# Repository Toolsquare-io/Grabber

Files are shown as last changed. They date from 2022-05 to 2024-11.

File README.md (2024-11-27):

# Tha Grabber
A machine to show what we can do with our [Toolsquare](www.toolsquare.io) units. 

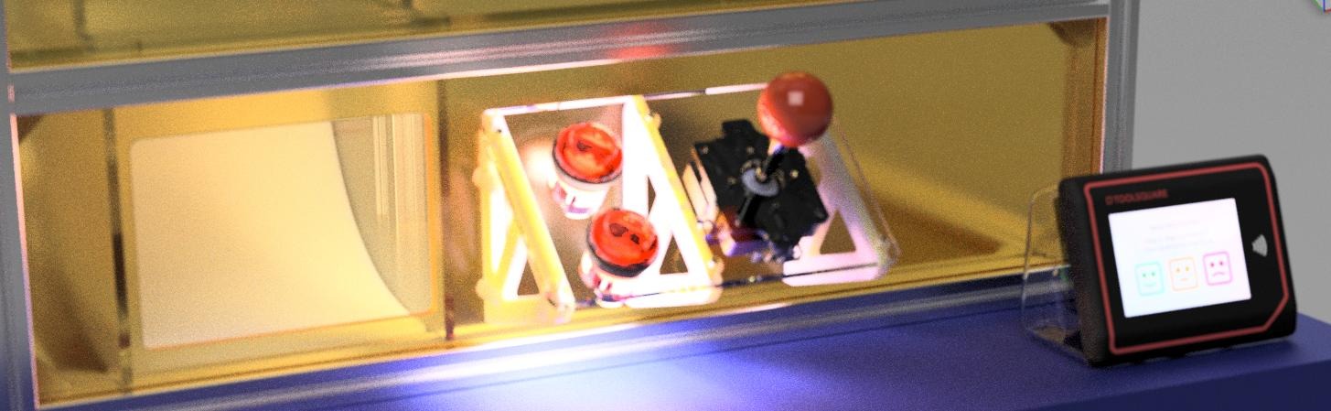
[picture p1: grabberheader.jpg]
Fusion render


## Timeline
### Deadline
* [Laborama](https://expo.laborama.be/nl/) 19 & 20 mei
* [Nerdland](https://www.nerdlandfestival.be/) 3, 4 & 5 juni

### Build timeline
* CAD approval -> 8th of April
---

**Everything below is draft and could change, keep those affected in the loop!**

---

## Requirements
* Dimensions footprint: 60x60cm
* Should reflect a Toolsquare machine: locked, idle, running. 
* Gadget max dimension: 14x12cm, height 7cm
* Should be easy to install by one person
* Should be able to run without supervision (so not too easy to break in) 
* Lights!

## The game
1. Unlock the machine using a Toolsquare unit or something else (a coin, a simple nfc reader,..)
2. Use the joystick to positon X and Y
3. Press a button to auto **lower the grabber, raise and dump the gadget**
5. Once a timout is reached the crane goes back to home and needs to be unlocked again

## BOM
The full [BOM](https://docs.google.com/spreadsheets/d/1Js6a-A9pP3j60k_G_hthX2zwbCBgAsaMytp7D8mz5XA/edit?usp=sharing)
* [Bosch-Rexroth](https://benl.rs-online.com/web/c/engineering-materials-industrial-hardware/structural-systems/) and connections
* [Optional Neopixels](https://www.adafruit.com/product/1138?length=1)
* ESP32
* [Linear Bearings](https://benl.rs-online.com/web/p/products/2346942/)
* [Linear Guide](https://benl.rs-online.com/web/p/products/4485449/) and cariage (https://benl.rs-online.com/web/p/products/3752445/)
* [Motors](https://www.amazon.nl/gp/product/B06Y2BSCL7/ref=ppx_yo_dt_b_asin_title_o00_s00?ie=UTF8&psc=1)

## CAD
[The Fusion model](https://a360.co/3V7IlZC)

## Inspirations
[CoreXY](http://corexy.com/theory.html)

CoreXY Math

## Electronics

Pinouts
CNCShield pinmapping

|  Function | Pin Number |  
|---|---|
|  Stepper X | |  
|  Stepper Y |  |  
|  Stepper Z  |  | 
|  Interlock X |  | 
|  Interlock Y  |  | 
|  Interlock Z  |  | 
|  JoyStick X  |  | 
|  JoyStick Y  |  |  
|  Button 1  |  | 
|  Button 2  |  | 
|  Button 1 LED  |  |
|  Button 2 LED  |  | 
|  NeoPixel  |  | 
|  Running Out  |  | 
|  Machine Lock  |  | 
|  Magnet Relais  |  |

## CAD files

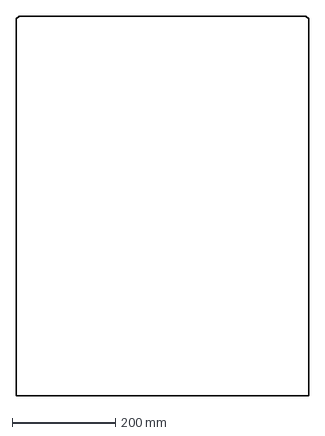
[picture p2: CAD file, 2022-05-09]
cad/production/TopFrontPlate.dxf
567.0 x 737.0 mm

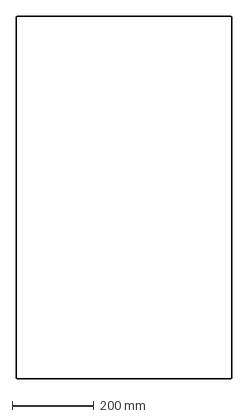
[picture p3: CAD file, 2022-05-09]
cad/production/RightPlate.dxf
527.0 x 887.0 mm

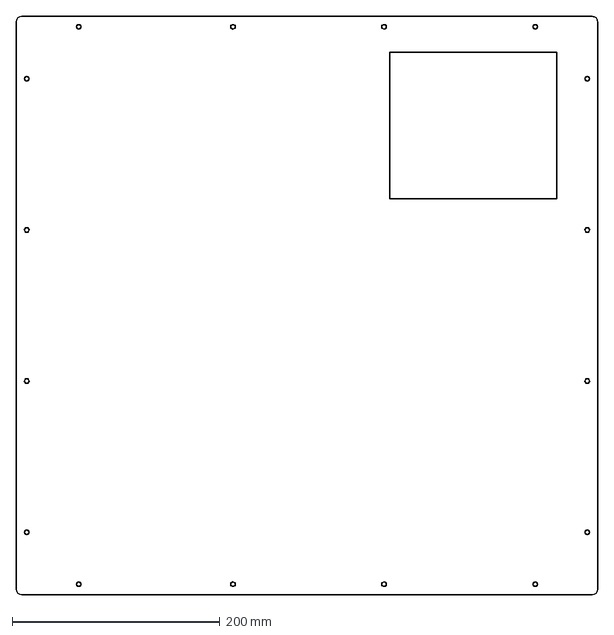
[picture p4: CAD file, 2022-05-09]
cad/production/GadgetFloorPlate.dxf
560.0 x 557.0 mm

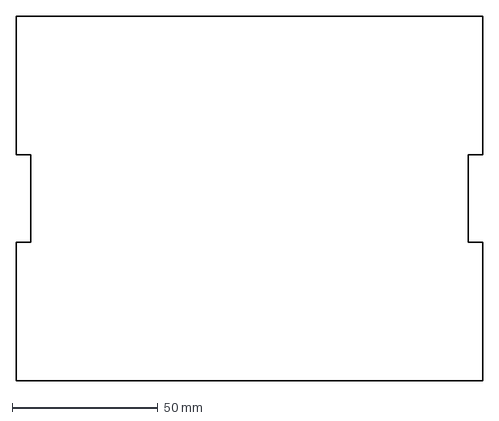
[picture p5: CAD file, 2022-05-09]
cad/production/GadgetTowerFront.dxf
160.0 x 125.0 mm

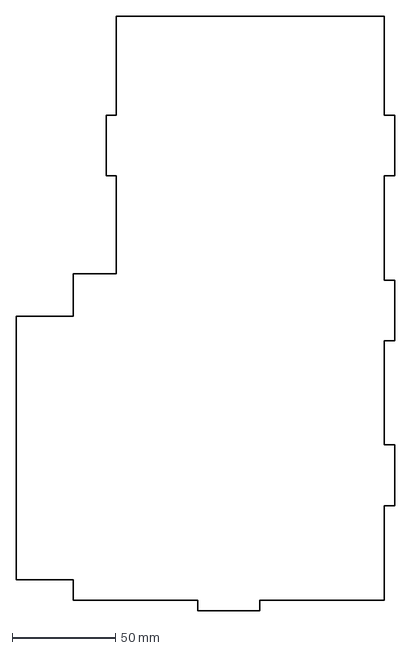
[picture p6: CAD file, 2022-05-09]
cad/production/GadgetTowerRight.dxf
183.5 x 288.5 mm

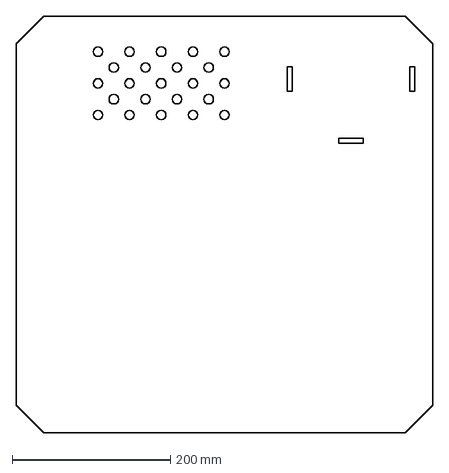
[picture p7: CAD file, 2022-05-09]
cad/production/BottomPlate.dxf
527.0 x 527.0 mm

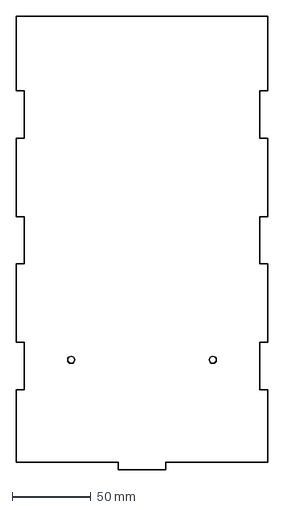
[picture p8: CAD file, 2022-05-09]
cad/production/GadgetTowerBack.dxf
160.0 x 288.5 mm

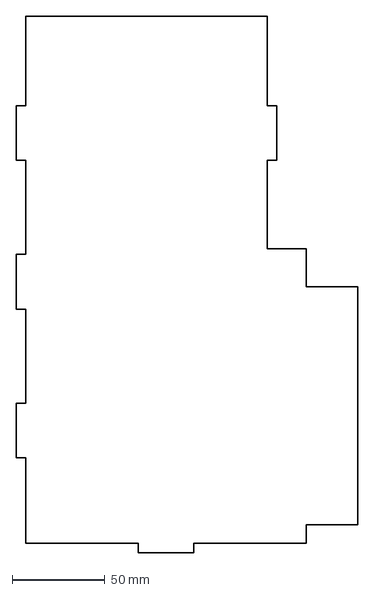
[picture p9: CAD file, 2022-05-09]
cad/production/GadgetTowerLeft.dxf
183.5 x 288.5 mm

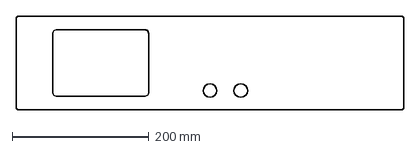
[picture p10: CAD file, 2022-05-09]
cad/production/FixedFrontPlate.dxf
567.0 x 137.0 mm

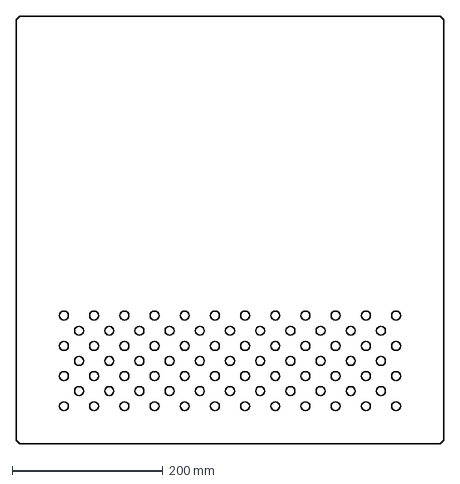
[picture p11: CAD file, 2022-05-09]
cad/production/TopPlate.dxf
567.0 x 567.0 mm

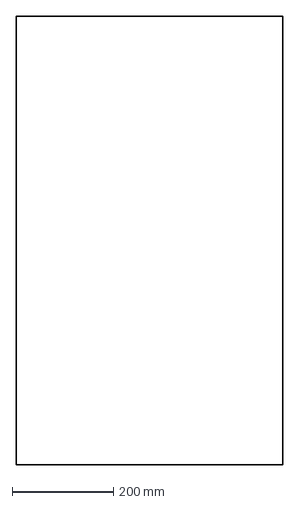
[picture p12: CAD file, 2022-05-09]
cad/production/LeftPlate.dxf
527.0 x 887.0 mm

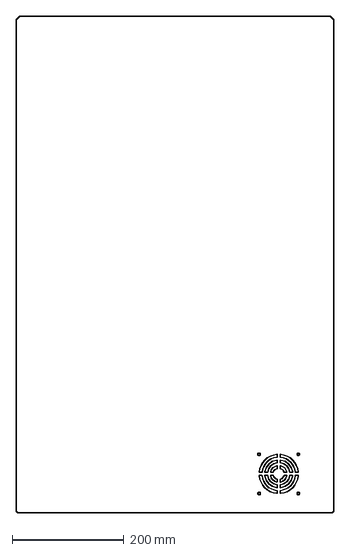
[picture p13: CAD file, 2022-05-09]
cad/production/BackPlate.dxf
568.0 x 888.0 mm

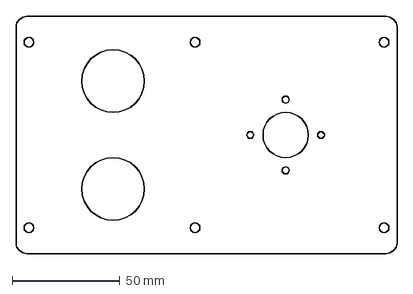
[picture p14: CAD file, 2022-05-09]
cad/production/Controller.dxf
176.6 x 110.0 mm

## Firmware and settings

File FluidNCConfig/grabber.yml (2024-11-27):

board: TMC2209 4X
name: TMC2209 XYZA
stepping:
  engine: I2S_STREAM
  idle_ms: 255
  pulse_us: 2
  dir_delay_us: 1
  disable_delay_us: 0

kinematics:
  corexy:

i2so:
  bck_pin: gpio.22
  data_pin: gpio.21
  ws_pin: gpio.17

axes:
  shared_stepper_disable_pin: NO_PIN
  
  x:
    steps_per_mm: 100
    max_rate_mm_per_min: 5000
    acceleration_mm_per_sec2: 100
    max_travel_mm: 298
    soft_limits: true
    homing:
      cycle: 2
      mpos_mm: 0
      positive_direction: false
      feed_mm_per_min: 400.000
      seek_mm_per_min: 1200.000
      settle_ms: 200
    
    motor0:
      limit_pos_pin: gpio.36:low
      hard_limits: false
      pulloff_mm: 10.000
      tmc_2209:
        uart:
          txd_pin: gpio.16
          rxd_pin: gpio.4
          baud: 115200
          mode: 8N1
        addr: 0
        r_sense_ohms: 0.110
        run_amps: 0.500
        hold_amps: 0.250
        microsteps: 16
        stallguard: 0
        stallguard_debug: true
        toff_disable: 0
        toff_stealthchop: 5
        toff_coolstep: 3
        run_mode: StealthChop
        homing_mode: StealthChop
        use_enable: true
        step_pin: i2so.2
        direction_pin: i2so.1
        disable_pin: i2so.0

    motor1:
      null_motor:

  y:
    steps_per_mm: 100
    max_rate_mm_per_min: 5000
    acceleration_mm_per_sec2: 100
    max_travel_mm: 325
    soft_limits: true

    homing:
      cycle: 3
      mpos_mm: 0
      positive_direction: false
      feed_mm_per_min: 400.000
      seek_mm_per_min: 1200.000
      settle_ms: 200
    
    motor0:
      limit_pos_pin: gpio.39:low
      hard_limits: false
      pulloff_mm: 10.00
      tmc_2209:
        addr: 1
        r_sense_ohms: 0.110
        run_amps: 0.500
        hold_amps: 0.250
        microsteps: 16
        stallguard: 0
        stallguard_debug: false
        toff_disable: 0
        toff_stealthchop: 5
        toff_coolstep: 3
        run_mode: StealthChop
        homing_mode: StealthChop
        use_enable: true
        step_pin: i2so.5
        direction_pin: i2so.4
        disable_pin: i2so.7

    motor1:
      null_motor:

  z:
    steps_per_mm: 100
    max_rate_mm_per_min: 5000
    acceleration_mm_per_sec2: 100
    max_travel_mm: 135
    soft_limits: true

    homing:
      cycle: 1
      mpos_mm: 0
      positive_direction: true
      feed_mm_per_min: 200.000
      seek_mm_per_min: 600.000
      settle_ms: 200

    motor0:
      limit_pos_pin: gpio.34:low
      hard_limits: false
      pulloff_mm: 10.000
      tmc_2209:
        addr: 2
        r_sense_ohms: 0.110
        run_amps: 0.500
        hold_amps: 0.250
        microsteps: 16
        stallguard: 0
        stallguard_debug: false
        toff_disable: 0
        toff_stealthchop: 5
        toff_coolstep: 3
        run_mode: StealthChop
        homing_mode: StealthChop
        use_enable: true
        step_pin: i2so.10
        direction_pin: i2so.9
        disable_pin: i2so.8

    motor1:
      null_motor:

spi:
  miso_pin: gpio.19
  mosi_pin: gpio.23
  sck_pin: gpio.18

sdcard:
  cs_pin: gpio.5
  card_detect_pin: NO_PIN

start:
  must_home: true

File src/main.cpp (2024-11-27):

#include <Arduino.h>
#include "logging.h"
#include "machineinputs.h"
#include "pinmapping.h"
#include "ledmadness.h"
#include "inputstates.h"

// creating the objects
uLog theLog;
machineInputs theInput;
pinmapping thePins;
ledmadness theLeds;

// forward declarations
// void echoSerial();
bool outputToSerial(const char* contents);
bool loggingTime(char* contents, uint32_t length);
void printHeartBeat();

void setup() {
    // configure output
    theLog.setColoredOutput(0U, true);        // enable colored output - remember to set 'monitor_flags = --raw' in platformio.ini    theLog.output(subSystem::general, loggingLevel::Error, "This is an error");           //
    Serial.begin(112500);
    Serial1.begin(115200);
    Serial1.setTimeout(50);
    theLog.setOutput(0U, outputToSerial);
    theLog.outputIsActive(true);

    // setting logginlevels
    theLog.setLoggingLevel(0U, loggingLevel::Debug);

    // setup start
    theLog.output(subSystem::general, loggingLevel::Info, "starting");        //

    theInput.initialize();
    theLeds.setup();

    delay(8000);
    Serial1.println("$H");
    delay(20000);
    Serial1.println("G01 X160 Y10 Z0 F2000");

  
}

void loop() {
    theInput.run();
    theLeds.run(theInput.getPosition());
    // echoSerial();
}

unsigned long timervalue;
unsigned long heartbeattimeout = 1000;

void printHeartBeat() {
    if (millis() - timervalue >= heartbeattimeout) {
        timervalue = millis();
        inputStates theState;
        theState = theInput.getPosition();
        switch (theState) {
            case inputStates::locked:
                Serial.println("locked");
                break;
            case inputStates::neutral:
                Serial.println("neutral");
                break;
            case inputStates::Xminus:
                Serial.println("x-");
                break;
            case inputStates::Xplus:
                Serial.println("x+");
                break;
            case inputStates::Yminus:
                Serial.println("y-");
                break;
            case inputStates::Zminus:
                Serial.println("z-");
                break;
            case inputStates::Zplus:
                Serial.println("z+");
                break;
            default:
                Serial.print(".");
                break;
        }
    }
}
// void echoSerial() {
//     while (Serial1.available()) {
//         theLog.output(subSystem::stepper, loggingLevel::Info, Serial1.read());
//     }
// }

// Logging helper functions
bool outputToSerial(const char* contents) {        // Step 3. Add a function which sends the output of the logging to the right hw channel, eg Serial port
    size_t nmbrBytesSent;
    nmbrBytesSent = Serial.print(contents);
    if (nmbrBytesSent > 0) {
        return true;
    } else {
        return false;
    }
}

bool loggingTime(char* contents, uint32_t length) {        // Step 4. Add a function which generates a timestamp string, so your logging events can get timestamped. Simple example is using millis()
    itoa(millis(), contents, 10);                          // convert millis to a string
    return true;
}

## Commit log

2022-04-26 Servo start
2022-04-28 pin change
2022-04-30 adding stepper class
2022-05-03 leds and steppers not blocking
2022-05-04 esp pin count
2022-05-09 cad and leds
    [BackPlate.dxf, BottomPlate.dxf, Controller.dxf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]
2022-05-11 leds fixed
2022-05-11 added leds and grab
    Buttons: I've added a breathe for the led's when machine is locked.
    Grabber: on setup a pwm signal is set to the grab intensity level. Grab is only possible when the machine is not locked.
2022-05-14 adding motor speeds
2022-05-16 Buttons working
2022-05-17 machine lock and 2nd led array
2022-06-01 Nr of leds adjusted
2022-11-22 Pinmapping changed
    [grabber.yml]
2022-11-29 Grabpin working
    [grabber.yml]
2023-03-09 Added lock
    [grabber.yml]
2024-11-27 Fixed the magnet
    The magnet ran hot because is wasn't turned off properly
    Also fixed the logging library so it can work with mysubsystems
    [main.cpp]
